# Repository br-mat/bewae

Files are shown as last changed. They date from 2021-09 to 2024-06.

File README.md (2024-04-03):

# Bewae - Bewässerungsprojekt v3.3

v3.3final versions are not stable (work in progress).

## About

Automatisiert Sensorgesteuerte Bewässerung mit Raspberry Pi & Arduino
<br>

**Ziele:**

+ Sensorgesteuerte Automatisierte Bewässerung der Balkonpflanzen
+ Speichern & Darstellung von Sensordaten
+ Überwachung & Steuerung von unterwegs
+ (Zukünftig) Abfrage von Wetterdaten & Bewässerung mit Machine Learning

## Inhalt:

- [Introduction (EN)](/README_EN.md)
- [Einleitung (DE)](#einleitung-de)
- [Steuerung des Systems](#steuerung-des-systems)
- [Setup](#setup)
- [Details](#details)
- [Bilder & Entstehung](#bilder--entstehung)

## Einleitung (DE)
Diese Version ist eher als Testversion zu sehen. <br>
Bei der bisherigen Aufarbeitung handelt es sich nicht um eine Schritt-für-Schritt-Anleitung. Es wird ein gewisses Grundwissen im Umgang mit Linux und Mikrokontrollern vorausgesetzt. Ziel ist es, lediglich einen Einblick in das Projekt zu geben und den Wiederaufbau im Frühjahr oder an neuen Standorten zu erleichtern. <br>

### Beschreibung

Zur Steuerung wird ein ESP-32 verwendet. Verschiedene Sensoren und Module erfassen eine Vielzahl von Daten, darunter Bodenfeuchtigkeits-, Temperatur-, Luftfeuchtigkeits- und Luftdruckdaten sowie Sonnenscheindauer. Diese Daten werden mithilfe eines InfluxDB-Clients an einen Raspberry Pi gesendet und in InfluxDB 2.0 gespeichert. <br>

Die Bewässerung folgt einem Zeitplan, der entweder mit vorprogrammierten Werten arbeitet oder über das Netzwerk gesteuert werden kann. Durch Einrichten eines VPNs (z.B. PiVPN) kann man auch von unterwegs seine Pflanzen im Auge behalten und bewässern. <br>

**Versorgung:**
Das System ist mit einem kleinen PV-Modul, einem Blei-Akku und einem kleinen 100l Wassertank ausgestattet. Je nach Temperatur muss nun nur noch einmal pro Woche daran gedacht werden, den Tank zu füllen. <br>

## Systemdiagramm

### V3.3 Abbildung:

 System Setup:                  | Solar Setup:
:-------------------------:|:-------------------------:
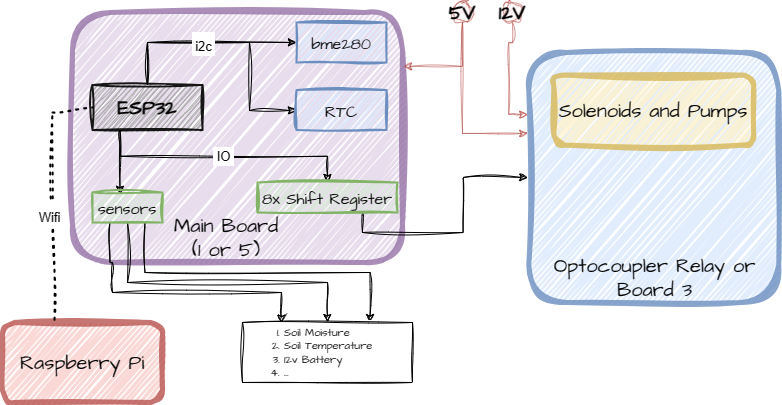
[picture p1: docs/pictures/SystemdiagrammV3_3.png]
System Systemdiagramm 3.3
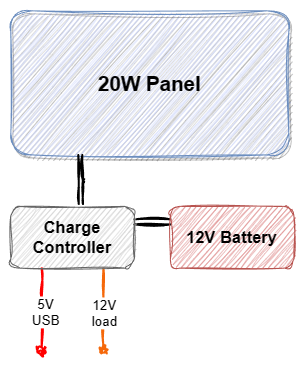
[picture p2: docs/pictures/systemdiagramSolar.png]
Solar Solar diagramm 3.3
 | 
zeigt grobe Skizzierung des Systems, Details zu Platinen siehe [(Details)](#details)

## Steuerung des Systems

### config.JSON

In dieser Datei befinden sich alle relevanten Einstellungen. Auf dem Controller wird diese Datei im Flash hinterlegt. Um auf Änderungen einfacher reagieren zu können, kann mit Node-Red (auf einem RaspberryPi) innerhalb des Netzwerks diese Datei zur Verfügung gestellt werden. Hierfür muss die Adresse in der connection.h angepasst werden.

Hinweis: Es ist auch möglich, ohne Verbindung zu einem RaspberryPi diese Datei zu verwenden, allerdings muss sie für Änderungen dann wieder neu aufgespielt werden.

### Steuerung der Bewässerung

Die Bewässerung wird mit den Einstellungen in der `config.JSON`-Datei gesteuert. Dabei werden zwei Variablen verwendet - timetable und water-time:

- 'timetable': Wird durch die ersten 24 Bit einer Integer-Zahl repräsentiert, wobei jedes Bit für eine Stunde des Tages steht. Um Platz zu sparen, wird es als Long Integer abgespeichert.
- 'water-time': Ist die Zeit (in Sekunden), die die jeweilige Gruppe bewässert wird. Hierbei können mehrere Ventile oder Ventil + Pumpe gleichzeitig gesetzt werden.

<br>

```cpp
// Beispiel-Zeitplan                           23211917151311 9 7 5 3 1
//                                              | | | | | | | | | | | |
unsigned long int timetable_default = 0b00000000000100000000010000000000;
//                                               | | | | | | | | | | | |
// Dezimale Darstellung: 1049600                22201816141210 8 6 4 2 0
//
```

Die Steuerung selbst kann auf folgenden Arten erfolgen:

- Config-Datei: Entweder lokal im Flash (SPIFFS), oder über Node-red bereitgestellt
- (currently not implemented) MQTT über W-LAN (App oder Pi) (noch nicht wieder implementiert)

<br>

Im File kann die Bewässerung wie im Beispiel unten konfiguriert werden:

```json
// JSON group template
{"group": {
    "Tomatoes": {         // name of grp
    "is_set":1,           // indicates status
    "vpins":[0,5],        // list of pins bound to group
    "water-time":10,      // water time in seconds
    "timetable":1049600,  // timetable (first 24 bit)
    "lastup":[0,0],       // runtime variable - dont touch!
    "watering":0          // runtime variable - dont touch!
    },
    .
    .
    .
  }
}
```

### Konfiguration der Sensoren:

Die Sensoren können mithilfe des `config.JSON` zu jeder Zeit verändert werden. Dabei sind einige Messfunktionen mit gängigen Sensoren implementiert. Es können auch noch Änderungen vorgenommen werden, um zurückgegebenen Werte zu modifizieren oder auch relative Messwerte (%) ausgegeben werden. <br>

Um einen Sensor korrekt zu konfigurieren ist es Notwendig eine Einzigartige ID als Json Key zu verwenden. Unter Diesem Key müssen noch 'name', 'field' und 'mode' vergeben werden. 'name' und 'field' entspricht dabei dem Eintrag in der DB unter dem der Messwert in InfluxDB zu finden ist. Implementierte 'mode' varianten können unten in der Tabelle entnommen werden, es kann erforderlich sein das noch weitere Dinge wie 'pin' etc. vorhanden sind.

Beispielkonfiguration:

```json
  "sensor": {
    "id00": {
      "name": "bme280",
      "field": "temp",
      "mode": "bmetemp"
    },
    .
    .
    .
    "id03": {
      "name": "Soil",
      "field": "temp",
      "mode": "soiltemp"
    },
    .
    .
    .
    "id08": {
      "name": "Soil",
      "field": "moisture",
      "mode": "vanalog",
      "vpin": 15,
      "hlim": 600,
      "llim": 250
    }
  },
  .
  .
  .
```

<br>

Konfiguration & Modifikatoren:
| Property | Description |
|---|---|
| `vpin` | Definiert Virtuellen Pin als input, für erweiterte Messfunktionen notwendig |
| `pin` | Definiert Normalen analogen Pin als input |
| `add` | (OPTIONAL) Addieren einer konstanten zum Ergebnis, optional wird nur bei >0 |
| `fac` | (OPTIONAL) Multiplizieren einer konstanten zum Ergebnis, optional wird nur bei >0 |
| `hlim` | (OPTIONAL) Obergrenze für relative Messung (%), optional wird nur bei >0 berücksichtigt |
| `llim` | (OPTIONAL) Untergrenze für relative Messung (%), optional wird nur bei >0 berücksichtigt |

<br>

Messfunktionen: <br>
| Measuring Mode | Description | Requirements |
|---|---|---|
| `analog` | reads analog pin | configured 'pin' in config.JSON |
| `vanalog` | reads virtual analog pin | configured 'vpin' in config.JSON |
| `bmetemp` | reads temperature from bme280 Sensor on Default address | Connected BME280 |
| `bmehum` | reads humidity from bme280 Sensor on Default address | Connected BME280 |
| `bmepress` | reads pressure from bme280 Sensor on Default address` | Connected BME280 |
| `soiltemp` | reads temperature from ds18b20 sensor from default 1 wire pin | Board need to have 1wire pin & connected Sensor |

<br>

## Setup Guide

### Mikrokontroller ESP32:

[Esp32 Code](./code/esp_32ard_bewae/) <br>

#### PlatformIO IDE

Stellen Sie zunächst sicher, dass PlatformIO in Visual Studio Code installiert ist. Dafür drücken Sie das 'Extensions' Icon in der linken Taskleiste und installieren 'PlatformIO IDE'. <br>

Öffnen Sie dann den Projektordner 'bewae' in VS Code. Schließen Sie als Nächstes Ihren ESP-32-Controller an. Zum Hochladen des Codes auf den ESP32 klicken Sie auf das Pfeilsymbol in der PlatformIO-Taskleiste. Das Gerät sollte automatisch erkannt werden, es kann nötig sein, die Boot-Taste während des Upload-Vorgangs zu drücken. Weiterhin ist es wichtig, das 'Filesystem' hochzuladen, dies kann mit dem Unterpunkt 'Upload Filesystem Image' der PlatformIO-Erweiterung gemacht werden. <br>

#### Config & WIFI (Optional)

Nun ist es wichtig, in den Dateien `connection.h` seine Zugangsdaten für das lokale Netzwerk einzutragen. <br>
Ebenfalls wären die IP des Systems worauf Node-red und die Datenbank installiert zu ändern. Sowie die dazugehörigen Daten. <br>
Weiters könnte noch die Adresse des Zeitservers zu ändern sein.  <br>

Für den Fall, dass keine Netzwerkverbindung möglich ist, sollte das Programm trotzdem funktionieren. Die Anpassung der Einstellungen ist dann allerdings schwieriger, da jedes Mal bei Änderungen das FileSystem neu hochgeladen werden muss. Außerdem muss die Zeit dann ebenfalls manuell gesetzt werden! Hierzu gibt es in der Helferklasse eine Funktion set_time. <br>

#### Config Hardware

Für die verschiedenen PCB-Layouts existieren unterschiedliche Hardware-Klassen. Diese leiten sich von der Helper-Klasse ab und schaffen eine Abstraktion der verwendeten Hardware. Dadurch wird es in Zukunft einfacher, andere Boards und sogar Mikrocontroller in das System zu integrieren.

Um die Konfiguration zu ändern, passen Sie bitte die folgenden Zeilen an Ihr verwendetes Board an:

##### ``main.cpp``
```cpp
// Initialisierung der Hardware Helper-Klasse
Helper_ExampleBoard HWHelper;
//Helper_config1_Board5v5 HWHelper;
```

##### ``Helper.h``
```cpp
// allowing to use HelperClass without having to create an instance of the class
extern ExampleBoard HWHelper;
```

Die verfügbaren Boards mit ihren Spezifikationen können Sie weiter unten finden.

### Raspberrypi

InfluxDB 2.0 benötigt ein 64-Bit-OS. Daher verwende ich einen Raspberry Pi 4B mit einem vollwertigen 64-Bit-Image.

#### Node-Red

How to [install](https://nodered.org/docs/getting-started/raspberrypi). <br>

Im Browser Your.Raspberry.Pi.IP:1880 Benutzer einrichten bzw. einloggen. Dann kann über das Web-Interface der [flow](/node-red-flows/flows.json) importiert werden. <br>
Öffnen Sie den Flow und klicken Sie doppelt auf den orangefarbenen 'read config'-Knoten. Ändern Sie den Pfad zu dem Pfad Ihrer Konfigurationsdatei.

#### InfluxDB 2.0

How to [install](https://docs.influxdata.com/influxdb/v2/install/?t=Raspberry+Pi). <br>
Influx kann auf zwei Arten aufgesetzt werden, entweder über das UI oder das CLI, Beschreibung dazu kann online gefunden werden (install link):

Set up InfluxDB through the UI
- With InfluxDB running, visit http://localhost:8086
- Click Get Started
- Set up your initial user
- Enter a Username for your initial user.
- Enter a Password and Confirm Password for your user.
- Enter your initial Organization Name.
- Enter your initial Bucket Name.
- Click Continue.

Die Berechtigungen für Buckets können recht einfach über das UI eingestellt werden und dazu dann ein Token generiert werden.

- In der Option 'Load Data' auf 'API TOKENS' klicken
- Klicken Sie auf 'Generate API TOKEN' -> Custom API Token
- Token-Beschreibung eingeben und Berechtigung (Write) wählen -> Auf 'Generate' klicken
- InfluxDB-Token nun in der `connection.h`-Datei ersetzen

---

Nun sollte alles vorbereitet sein. Die Konfigurationsdatei (`config.JSON`) kann nach Bedarf angepasst werden, dazu einfach die benötigten Funktionen (siehe Tabellen) wie im Beispiel gezeigt konfigurieren. <br>

Falls ein Relais-Modul verwendet wird mit invertierter Logik besteht die Option, die Ausgänge des Shift Registers zu invertieren, dazu in der `config.h`-Datei INVERT_SHIFTOUT auf true setzen. <br>
Weiterhin können noch Flags gesetzt werden, die das Debugging erleichtern. <br>

## Details

### Platinen

Die Schaltungen wurden mit Fritzing erstellt, die Steckbrettansicht bietet gute Übersicht und eignet sich ideal für Prototypen. Ab einer gewissen Größe des Projekts ist Fritzing allerdings nicht mehr ideal. Gerber-Dateien sind vorhanden. Für die Fritzing-Dateien ist lediglich die Platinenansicht relevant. Alle Boards verwenden den ESP-32 als Mikrocontroller. <br>

 Board 1:                  | Board 3:                  | Board 5:
:-------------------------:|:-------------------------:|:-------------------------:
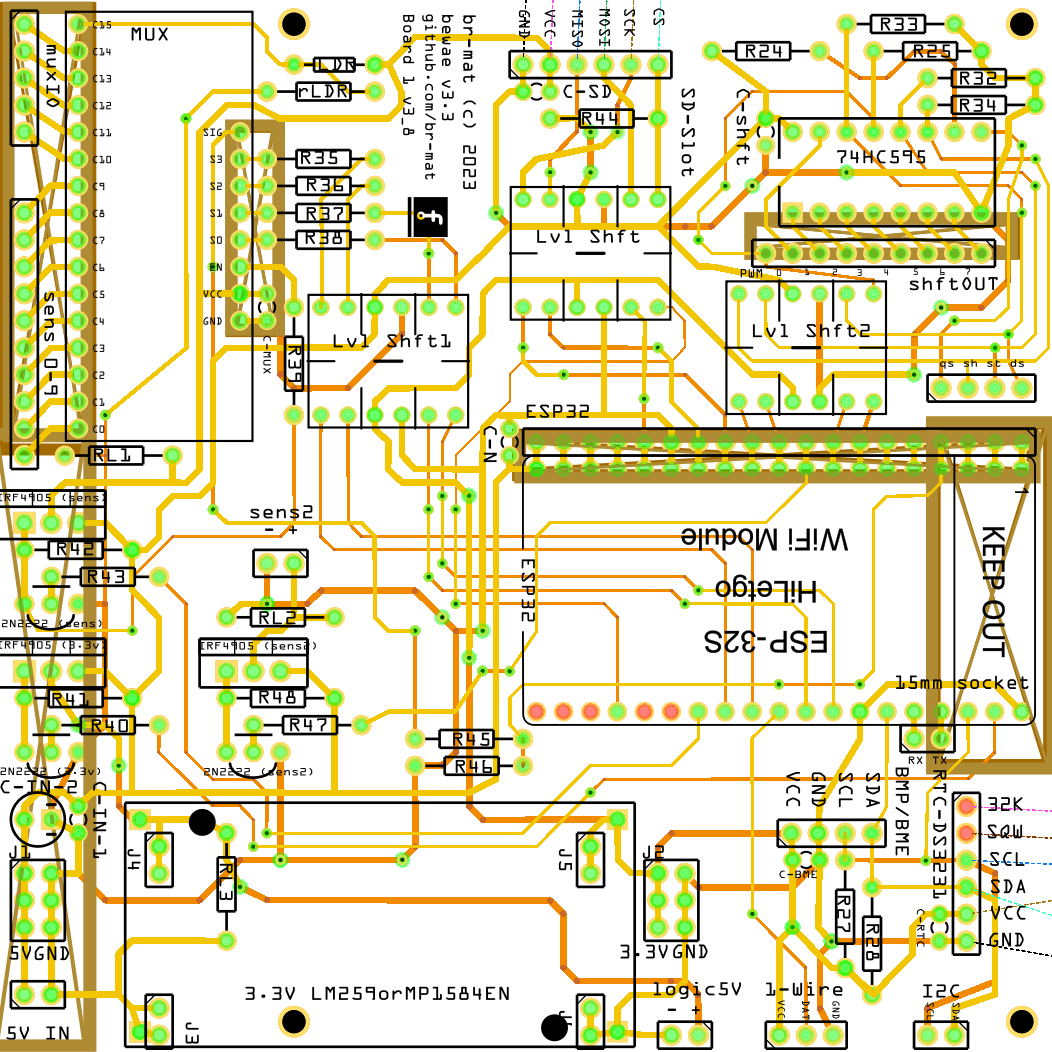
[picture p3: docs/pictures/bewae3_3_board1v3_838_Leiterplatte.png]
Board1
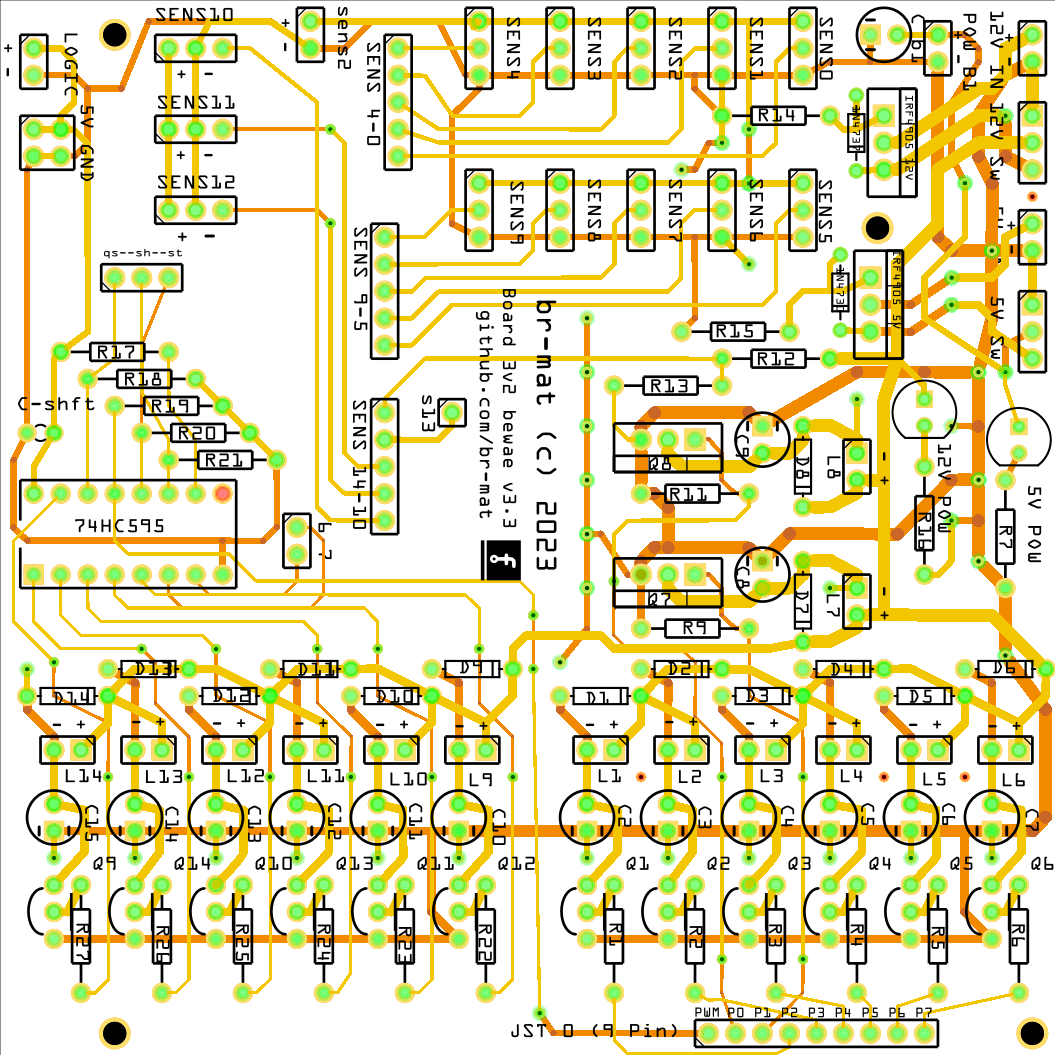
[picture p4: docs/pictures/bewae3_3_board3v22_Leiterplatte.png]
Board3
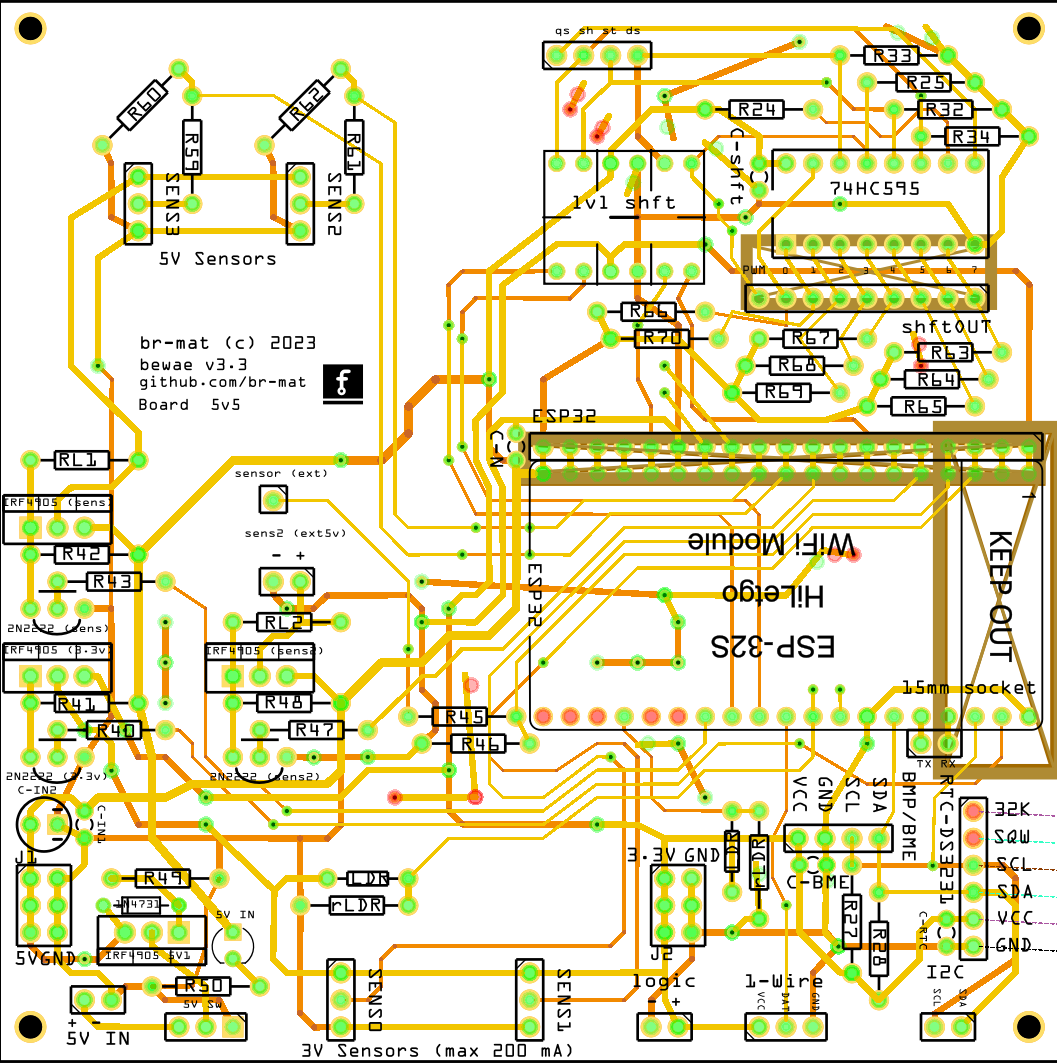
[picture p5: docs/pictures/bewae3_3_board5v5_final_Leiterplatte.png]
Board5
 |  | 
Main Board (Älteres testboard) | Extention Board | Main Board (neustes) <br> 

Steuerung der Ventile entweder über Optokoppler Relais (bis zu 8x mit adaption mehr) oder externe Beschaltung Board 3 und ähnliche. Die Ansteuerung ist über das Schieberegister (74hc595) vorgesehen.

#### **bewae3_3_board1v3_838.fzz** Hauptplatine (PCB)

Große Hauptplatine. Erfordert Board 3 oder externe Beschaltung für große Anzahl an analoger Sensoren. <br> Platz für bis zu 16 analoge Sensoren sowie BME280- und RTC-Modul über I2C. 8 Pins für Ventile/Pumpen (erweiterbar). Diese können entweder über Relais oder dem PCB Board 3 einfach verwendet werden.<br>

#### **bewae3_3_board3v22.fzz** als Erweiterung (PCB)

Als Erweiterung gedacht. Hat den Zweck, Steckplätze für Sensoren und weitere Verbraucher bereitzustellen. Zur Erweiterung der 8 Pins der Hauptplatine kann das Schieberegister verwendet werden. Insgesamt 16 Steckplätze für Sensoren inklusive Versorgung, sowie 2 Pumpen (*12V*) und 10 kleinere Ventile (*12V*).<br>

#### **bewae3_3_board5v5_final.fzz** als Hauptplatine (PCB)

Kleinere Hauptplatine (neueste). bietet die möglichkeit für eine Begrenzte anzahl an analogen Sensoren direkt am Board.
Verzichtet jedoch auf eine größere Anzahl an (analogen) Sensoranschlüssen. <br> 8 Pins für Ventile/Pumpen (mit Schieberegister erweiterbar). Platz für 2x 5V Sensoren, 2x 3V Sensoren, 1x LDR, I2C-Bus, 1-Wire-Bus. BME280- und RTC-Modul sind ebenfalls vorgesehen.<br>

### aktueller Aufbau

- ESP32 Board 1 & 3; Esp32 Board 5
- RaspberryPi 4 B (4GB)
- 10 Ventile 12V
- 2 Pumpen (aktuell nur eine 12V im Betrieb)
- 16 Analoge/Digitale Pins für Sensoren & andere Messungen (Bodenfeuchte, Photoresistor, etc.)
- BME280 Temperatur/Luftfeuchtigkeit/Druck Sensor
- RTC DS3231 Real Time Clock
- Bewässerungs Kit: Schläuche, Sprinkler, etc.
- 20W 12V Solar Panel
- 12 Ah 12V Bleiakku
- Solarladeregler

## Bilder & Entstehung

**Entstehung:** <br>

Das Projekt entstand aus einer mehrwöchigen Abwesenheit, während der die Balkonpflanzen ohne Versorgung gewesen wären. Die Pflanzen sollten mithilfe eines Bewässerungssets, Schläuchen, ein paar Düsen und einer Pumpe am Leben gehalten werden. Eine reguläre Bewässerung wie bei einer Zeitschaltuhr erschien mir jedoch zu langweilig, und mein Interesse an einem kleinen Bastelprojekt war geweckt. Kapazitive Bodenfeuchtesensoren und 4 kleine 12V Ventile wurden schnell bestellt, da ich zu Hause genügend Arduinos hatte. So kam es innerhalb einer Woche zur [Version 1](#v1), und das Überleben der Pflanzen war gesichert. Aus der Not heraus entstand ein Projekt, das mich eine Weile beschäftigte, und durch kontinuierliche Erweiterung und Verbesserung erfüllt es nach momentanem Stand weit mehr, als ursprünglich geplant. <br>
<br>

Zum Abschluss eine kleine Sammlung von Fotos über mehrere Versionen des Projekts, die im Laufe der Zeit entstanden sind:

### V3

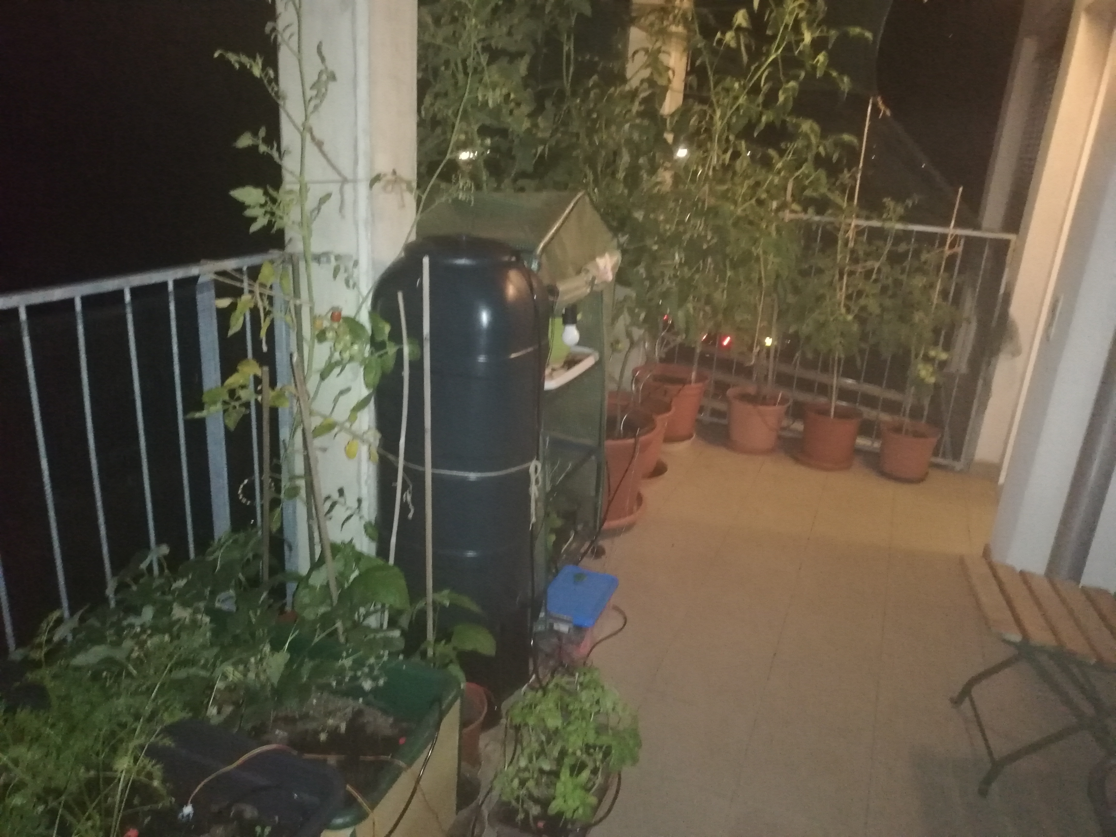
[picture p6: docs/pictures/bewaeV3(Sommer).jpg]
Bild
 <br>
Bild <br>
Bild <br>
Bild <br>

### V2

Bild <br>

### V1

Bild <br>
Bild <br>

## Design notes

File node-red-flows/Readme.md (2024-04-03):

flows.json:
This flow hosts a file to get request it.
In order to use flows.json you have to change the paths where the file is located.

bewaeConfigPageFlow.json:
This hosts a config web page where you can add and change values.
Change the path of the files of write and read -file nodes.

The flow contains a page to host the config file. (replacing older flows.json implementation)

Check for any other necessary changes.

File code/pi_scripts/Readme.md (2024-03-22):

This document provides a brief overview of how to use the following scripts. They are designed to run on a Raspberry Pi or a similar device using crontab.

1. store_weather_data.py:
   - This script collects data from OpenWeatherMap and stores it in a local InfluxDB instance (version 2.x).
   - Note: It is currently not required for functionality.

2. estimate_water_loss.py:
   - The purpose of this script is to retrieve forecast data from OpenWeatherMap.
   - It calculates an estimated total evaporation loss in milliliters per hour.
   - This function is intended to be executed daily.
   - The results can be used to automate plant irrigation if configured correctly, considering plant size and soil area.

3. hourlisttoBIN.py (to be removed soon):
   - This script converts a list of hours into a single number, which is used in the timetable.

4. old-config-to-JSON.py (to be removed soon):
   - Use this script to convert an old configuration format to the new one.

Additional files:
5. irrigation_example.JSON: This file provides an example configuration for the irrigation system.

6. monitoring_config.JSON: In this file, you can fill in details about the connection to InfluxDB, API keys, and other relevant settings.

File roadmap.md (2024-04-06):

This is a small roadmap to help me remember what I am working on.

To-do:
- Implement config web page (RaspberryPi)
- Integrate new configuration into the system (ESP32)
- Add OpenWeather forecast script to the Pi
- Reimplement dynamic watering controlled by Raspberry Pi
- Updated documentation

Open problems:
- Sensor rail needs 5V, not 3V! (Currently hooked onto logic switch 3.3V)

Future ideas:
- Add display and interface menu
- Using machine learning to controll watering process based on collected data
- Implement an app (configuration of sensors and groups)
- Add option to upload config file via bluetooth

Changes:
- Added OpenWeather scripts (saving current conditions and air condition to InfluxDB)
- Added corresponding .sh launcher files
- Added ESP32 build
- Added a second circuit to handle pumps and solenoids
- Updated (and tested) main circuit, corrected bugs and problems on ESP32 build
- Updated English translation of new version
- Added a new IrrigationController class
- Implemented a config file system using SPIFFS
- Implemented HTTP GET functionality to update config file
- Added Node-RED flow to provide config file
- Reworked circuit boards included new ones
- fixed reverse voltage protection
- Removed SD slot

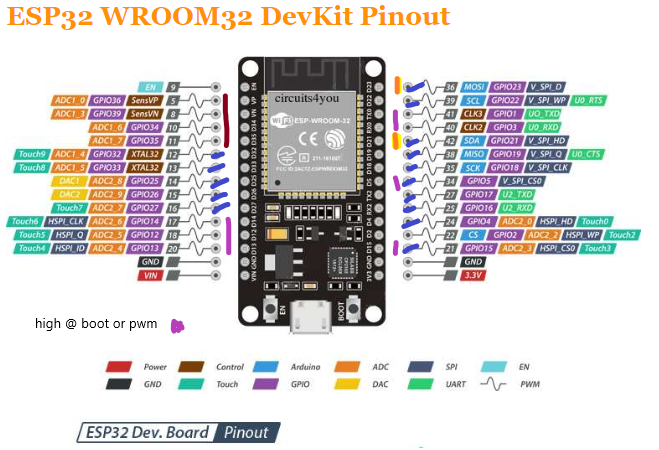
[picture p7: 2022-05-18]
code/esp_32ard_bewae/esp32-wroom-pinout-project.PNG

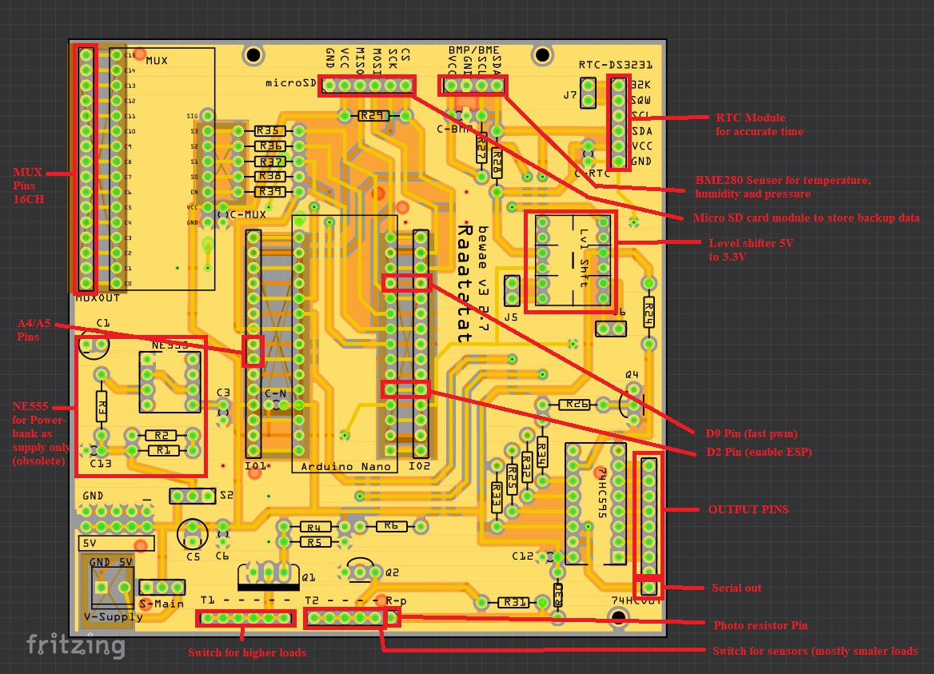
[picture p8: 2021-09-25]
docs/pictures/bewae_v3_1.png

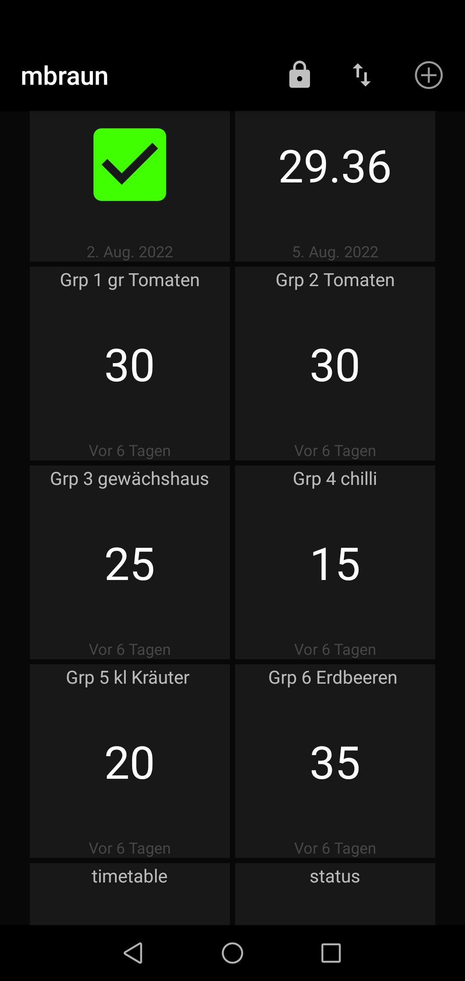
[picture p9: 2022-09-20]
docs/pictures/watering-config.jpg

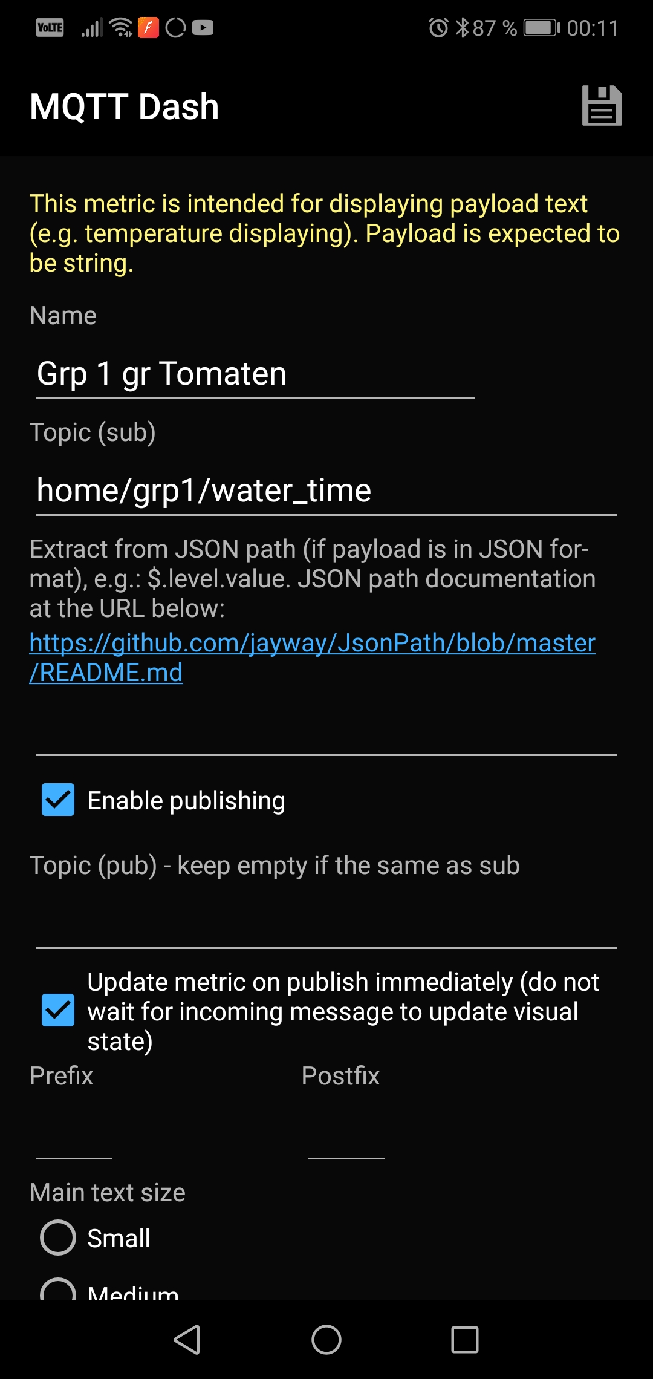
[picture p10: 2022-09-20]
docs/pictures/mqtt-app.jpg

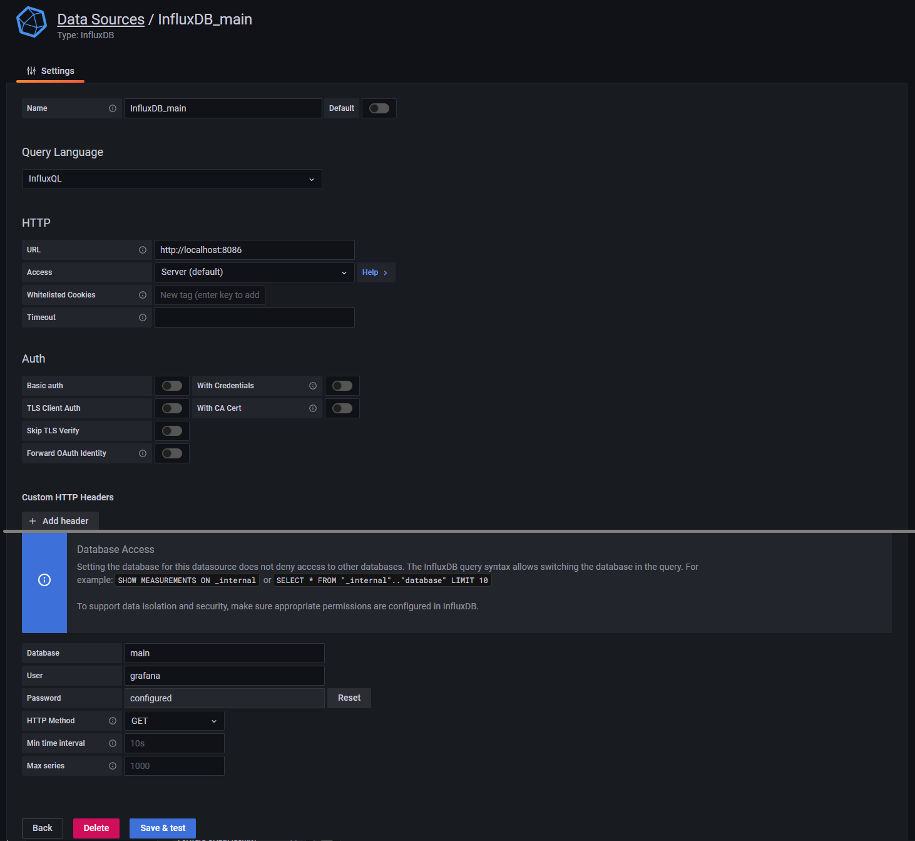
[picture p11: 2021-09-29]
docs/pictures/datasources.png

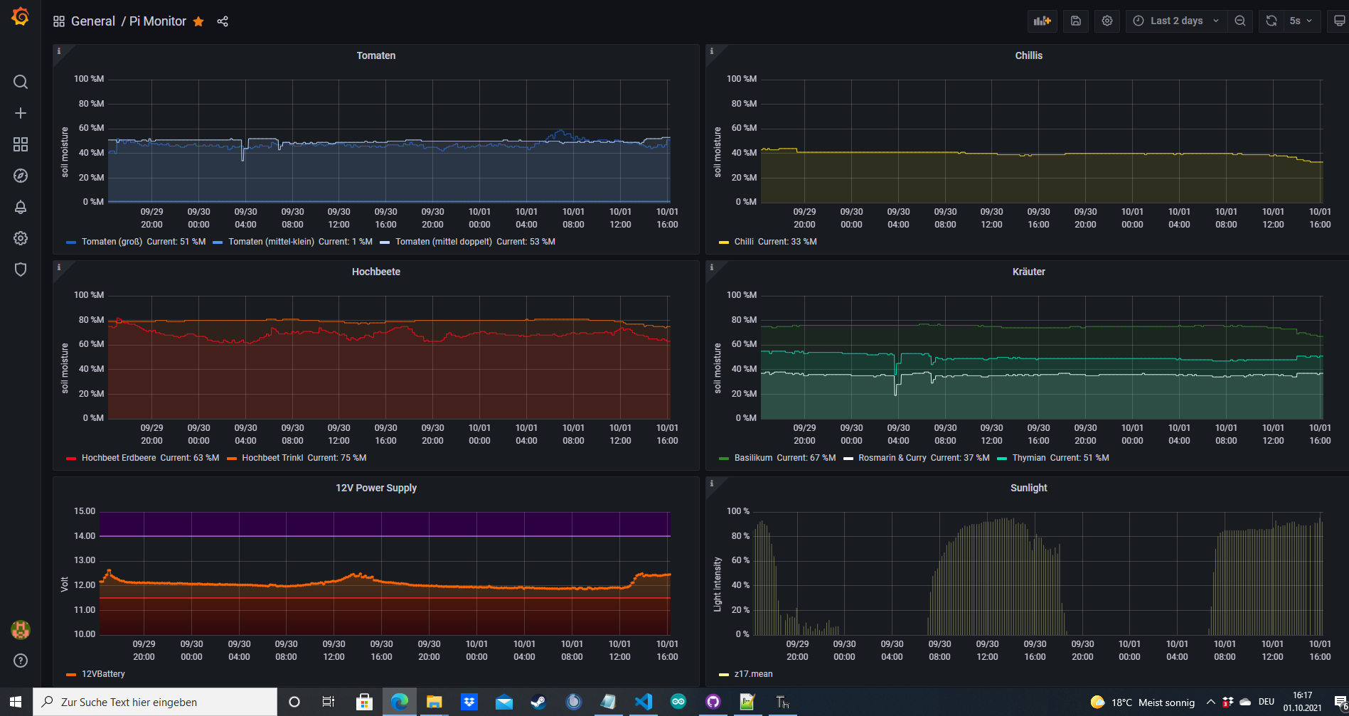
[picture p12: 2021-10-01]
docs/pictures/grafanarainyday.png

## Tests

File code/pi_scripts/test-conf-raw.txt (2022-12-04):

group
99 master 0 0
0 Tom1 100 0
1 Tom2 80 0
2 Gewa 30 0
3 Chil 40 0
4 Krtr 20 0
5 Erdb 50 0

switches
sw6 1
sw0 1
sw1 0
sw2 0

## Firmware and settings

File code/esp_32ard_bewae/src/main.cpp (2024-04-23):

////////////////////////////////////////////////////////////////////////////////////////////////////////////////////////
//
// br-mat (c) 2023
// email: matthiasbraun@gmx.at
//
// This is the main source file for the irrigation system. It is responsible for monitoring all sensor values,
// handling the watering procedure, and communicating with the Raspberry Pi to get and send data.
//
////////////////////////////////////////////////////////////////////////////////////////////////////////////////////////

//Standard
#include <Arduino.h>
#include <Wire.h>
#include <SPIFFS.h>
#include <OneWire.h>

//external
#include <Adafruit_Sensor.h>
#include <Adafruit_BME280.h>
#include <WiFi.h>
#include <PubSubClient.h>
#include <ArduinoJson.h>
#include <DallasTemperature.h>

//custom
#include <connection.h>
#include <Helper.h>
#include <IrrigationController.h>
#include <SensorController.h>
#include <SwitchController.h>
#include <config.h>

using namespace std;

//######################################################################################################################
//----------------------------------------------------------------------------------------------------------------------
//---- GLOBAL VARIABLES AND DEFINITIONS --------------------------------------------------------------------------------
//----------------------------------------------------------------------------------------------------------------------
//######################################################################################################################
//important global variables
//byte sec_; byte min_; byte hour_; byte day_w_; byte day_m_; byte mon_; byte year_; // containing time variables

struct tm oldtimeMark; // timemark

unsigned long nextActionTime = 0; // timestamp variable

bool thirsty = false; // marks if a watering cycle is finished

//timetable example
//                                             2523211917151311 9 7 5 3 1
//                                              | | | | | | | | | | | | |
//unsigned long int timetable_default = 0b00000000000000000000010000000000;
//                                               | | | | | | | | | | | | |
//                                              2422201816141210 8 6 4 2 0
unsigned long int timetable = 0; // holding info at which hour system needs to do something

// Setup a oneWire instance to communicate with any OneWire device
OneWire oneWireGlobal(oneWireBus);

// Pass our oneWire reference to Dallas Temperature sensor 
DallasTemperature soilsensorGlobal(&oneWireGlobal);

// use I2C interface
Adafruit_BME280 bme;

// initialise WiFi
WiFiClient wificlient;

// initialise Hardware Helper class
Helper_config1_Board5v5 HWHelper;
//Helper_config1_Board5v5 HWHelper;

// Create a BasicSensor instance
BasicSensor Sensors(&HWHelper, &bme, soilsensorGlobal);

// Create an instance of the InfluxDBClient class with the specified URL, database name and token
InfluxDBClient influx_client(INFLUXDB_URL, INFLUXDB_ORG, INFLUXDB_DB_NAME, INFLUXDB_TOKEN);

//######################################################################################################################
//----------------------------------------------------------------------------------------------------------------------
//---- SOME ADDITIONAL FUNCTIONS ---------------------------------------------------------------------------------------
//----------------------------------------------------------------------------------------------------------------------
//######################################################################################################################

// Task implementation can be found on bottom of code

// containing irrigation implementation, returns false if irrigation finished else true
bool irrigationTask();
// sensoring implementation, returns timestamp of next event in UL
long sensoringTask();
// powering down system, returning false when theres something to do else true!
bool checkSleepTask();

//######################################################################################################################
//----------------------------------------------------------------------------------------------------------------------
//---- SETUP -----------------------------------------------------------------------------------------------------------
//----------------------------------------------------------------------------------------------------------------------
//######################################################################################################################

void setup() {
///////////////////////////////////////////////////////////////////////////////////////////////////////////////////////////
// init
///////////////////////////////////////////////////////////////////////////////////////////////////////////////////////////
  //setCpuFrequencyMhz(80);
  // configure low power timer
  esp_sleep_enable_timer_wakeup(TIME_TO_SLEEP * uS_TO_S_FACTOR);

///////////////////////////////////////////////////////////////////////////////////////////////////////////////////////////
// configure pin mode
///////////////////////////////////////////////////////////////////////////////////////////////////////////////////////////
  HWHelper.setPinModes();

///////////////////////////////////////////////////////////////////////////////////////////////////////////////////////////
// initialize serial
///////////////////////////////////////////////////////////////////////////////////////////////////////////////////////////
  Serial.begin(9600);
  delay(1);
  #ifdef DEBUG
  Serial.println("Hello!");
  #endif

///////////////////////////////////////////////////////////////////////////////////////////////////////////////////////////
// initialize SPIFFS
///////////////////////////////////////////////////////////////////////////////////////////////////////////////////////////
  if (!SPIFFS.begin(true)) {
    #ifdef DEBUG
    Serial.println(F("An Error has occurred while mounting SPIFFS"));
    #endif
    return;
  }
  #ifdef DEBUG
  unsigned int totalBytes = SPIFFS.totalBytes();
  unsigned int usedBytes = SPIFFS.usedBytes();
  Serial.print("Total space: ");
  Serial.println(totalBytes);
  Serial.print("Used space: ");
  Serial.println(usedBytes);
  #endif

  /*
  fs::File file = SPIFFS.open(CONFIG_FILE_PATH);
  if(!file){
    #ifdef DEBUG
    Serial.println("Failed to open file for reading");
    #endif
    return;
  }
  file.close();*/

///////////////////////////////////////////////////////////////////////////////////////////////////////////////////////////
// initialize bme280 & ds18b20 sensor
///////////////////////////////////////////////////////////////////////////////////////////////////////////////////////////
  HWHelper.enablePeripherals();
  HWHelper.enableSensor();

  // test bme280
  delay(300); // giving some time to handle powerup of devices

  #ifdef DEBUG
  Serial.println(F("BME280 Sensor event test"));
  if (!bme.begin(BME280_I2C_ADDRESS)) {
    Serial.println(F("Warning: Could not find a valid BME280 sensor, check wiring!"));
  }
  else{
    float temp_test = bme.readTemperature();
    Serial.print(F("Temperature reading: ")); Serial.println(temp_test);
  }
  delay(10);

  // test ds18b20
  soilsensorGlobal.begin();
  delay(100);

  // Request temperature
  soilsensorGlobal.requestTemperatures();
  delay(5);
  // Read temperature from DS18B20 sensor
  float temperatureC = soilsensorGlobal.getTempCByIndex(0);
  Serial.print("Test DS18B20: "); Serial.println(temperatureC);
  #endif

///////////////////////////////////////////////////////////////////////////////////////////////////////////////////////////
// init time and date
///////////////////////////////////////////////////////////////////////////////////////////////////////////////////////////
  HWHelper.wakeModemSleep();
  delay(1);
  //uncomment if want to set the time (NOTE: only need to do this once not every time!)
  //HWHelper.set_time(00,56,18,01,11,9,23);
  //seting time (second,minute,hour,weekday,date_day,date_month,year)
  struct tm localTime = HWHelper.readTimeNTP();

  // automatically set time (requires WIFI access!!)
  struct tm local = HWHelper.readTimeNTP();
  if(HWHelper.verifyTM(local)){
    #ifdef DEBUG
    Serial.println(F("Info: Synched time!"));
    #endif
    HWHelper.setTime(local);
  }
  #ifdef DEBUG
  else{
    Serial.println(F("Setup Warning: Could not verify time!"));
  }
  #endif

  delay(100);
  //initialize global time
  bool condition = HWHelper.readTime(&oldtimeMark);
  delay(30);

///////////////////////////////////////////////////////////////////////////////////////////////////////////////////////////
//init Irrigation Controller instance and update config
///////////////////////////////////////////////////////////////////////////////////////////////////////////////////////////
  HWHelper.wakeModemSleep();
  delay(1);
  // update the config file stored in spiffs
  // in order to work a RasPi with node-red and configured flow is needed
  HWHelper.syncConfig();
  // TEST DEVICE CONFIGURATION
  SwitchController status_switches(&HWHelper); // initialize switch class

Serial.print("Free heap memory: ");
Serial.println(ESP.getFreeHeap());
Serial.print("Test DEVICE CONFIG!");
DynamicJsonDocument doc(512);
Serial.print("Free heap memory: ");
Serial.println(ESP.getFreeHeap());
String p = IRRIG_CONFIG_PATH; // Make sure IRRIG_CONFIG_PATH is defined somewhere
String p2 = JSON_SUFFIX;
String filePath = p + p2; // Concatenate to form the file path
DynamicJsonDocument jsonDoc = HWHelper.readConfigFile(filePath.c_str());
Serial.println("TESTING FILE RETURNS!");
Serial.println(jsonDoc.isNull());
String f_jsonDoc;
serializeJson(jsonDoc, f_jsonDoc);
Serial.println("Irrig file: ");
Serial.println(f_jsonDoc);

Serial.print("Free heap memory: ");
Serial.println(ESP.getFreeHeap());

  HWHelper.system_sleep(); //power down prepare sleep
  delay(100);

}

//######################################################################################################################
//----------------------------------------------------------------------------------------------------------------------
//---- MAIN PROGRAM LOOP -----------------------------------------------------------------------------------------------
//----------------------------------------------------------------------------------------------------------------------
//######################################################################################################################
void loop(){
////////////////////////////////////////////////////////////////////////////////////////////////////////////////////////
// start & sleep loop
////////////////////////////////////////////////////////////////////////////////////////////////////////////////////////

// manage sleep and updating of configuration
while(checkSleepTask()){
}
Serial.print(F("INIT SWITCHES:"));
SwitchController status_switches(&HWHelper); // initialize switch class
//status_switches.updateSwitches(); // get called when initialized

// print system status
#ifdef DEBUG
Serial.println(F("Config: ")); Serial.print(F("Main switch: ")); Serial.println(status_switches.getMainSwitch());
Serial.print(F("Irrigation switch: ")); Serial.println(status_switches.getIrrigationSystemSwitch());
Serial.print(F("Measurement switch: ")); Serial.println(status_switches.getDatalogingSwitch());
Serial.print(F("Timetable: ")); Serial.println(timetable, BIN);
#endif

////////////////////////////////////////////////////////////////////////////////////////////////////////////////////////
// collect & send data
////////////////////////////////////////////////////////////////////////////////////////////////////////////////////////
#ifdef DEBUG
Serial.print(F("Datalogphase: ")); Serial.println(millis() > nextActionTime);
Serial.print(F("Next action time: ")); Serial.println(nextActionTime);
#endif
//if(true)
if((status_switches.getDatalogingSwitch()) && (millis() > nextActionTime))
{
  // Sensoring implementation
  nextActionTime = sensoringTask() + measure_intervall; // sensoring task returns finishing timestamp
}
else{
  nextActionTime = millis() + measure_intervall *2; // set a min delay (2 times longer)
}

////////////////////////////////////////////////////////////////////////////////////////////////////////////////////////
// watering - return true if finished
////////////////////////////////////////////////////////////////////////////////////////////////////////////////////////
if(status_switches.getIrrigationSystemSwitch()){ // always enter checking, timing is handled by irrigation class
  irrigationTask();
}
#ifdef DEBUG
else{
Serial.print(F("Irrigation not set, satus: ")); Serial.println(status_switches.getIrrigationSystemSwitch());
}
#endif

////////////////////////////////////////////////////////////////////////////////////////////////////////////////////////
// end loop
////////////////////////////////////////////////////////////////////////////////////////////////////////////////////////

#ifdef DEBUG
Serial.println(F("--- End loop! ---"));
#endif
}
//######################################################################################################################
//----------------------------------------------------------------------------------------------------------------------
//---- MAIN PROGRAM END -------------------------------------------------------------------------------------------------
//----------------------------------------------------------------------------------------------------------------------
//######################################################################################################################



////////////////////////////////////////////////////////////////////////////////////////////////////////////////////////
// sensoring - returns timestamp of next event
////////////////////////////////////////////////////////////////////////////////////////////////////////////////////////
long sensoringTask(){
  #ifdef DEBUG
  Serial.println();
  Serial.println(F("enter datalog phase"));
  #endif

  if(!PUBDATA){
    #ifdef DEBUG
    Serial.println();
    Serial.println(F("Not mearuring Data! Flag set to false."));
    #endif
    return millis();
  }

  // turn on additional systems
  HWHelper.enablePeripherals();
  HWHelper.enableSensor();
  // shutdown wifi to free up adc2 pins!
  HWHelper.disableWiFi();
  delay(500); // give time to balance load

  // Create data vector to collect and publish later
  std::vector<SensorData> dataVec;
  std::vector<SensorData> dataVecTest;

  DynamicJsonDocument configf(CONF_FILE_SIZE);
  String path = String(SENS_CONFIG_PATH) + String(JSON_SUFFIX);
  configf = HWHelper.readConfigFile(path.c_str());
  JsonObject obj;

  //float test = Sensors.onewirehandler();
  //Serial.print("ds18b20 temp: "); Serial.println(test);

  // handle analog pins
  obj = configf.as<JsonObject>();

  if(obj){
    for (JsonObject::iterator it = obj.begin(); it != obj.end(); ++it){
      String id = it->key().c_str();
      JsonObject sensorConfig = it->value().as<JsonObject>();
      // create & fill data
      SensorData data = Sensors.measurePoint(&HWHelper, id, sensorConfig);
      // Add the new SensorData object to the vector
      dataVecTest.push_back(data);
    }
  }

  // reconnect to wifi
  HWHelper.connectWifi();
  // Publish data vector
  bool success = Sensors.pubVector(&influx_client, dataVecTest);
  //bool success = false; //DEBUG
  #ifdef DEBUG
  if(success){
    Serial.println(F("All data published!"));
  }
  else{
    Serial.println(F("Warning: Problem occured while publishing data vector!"));
  }
  #endif

  // shut down addidional systems
  HWHelper.disablePeripherals();
  HWHelper.disableSensor();

  return millis(); // finishing timestamp
}



////////////////////////////////////////////////////////////////////////////////////////////////////////////////////////
// watering - return true if NOT fnished
////////////////////////////////////////////////////////////////////////////////////////////////////////////////////////
bool irrigationTask(){
//thirsty = true; //uncoment for testing only
  HWHelper.enablePeripherals();

  #ifdef DEBUG
  Serial.println(F("Enter watering phase"));
  #endif
  delay(30);

  // load config file
  String path = String(IRRIG_CONFIG_PATH) + String(JSON_SUFFIX);
  DynamicJsonDocument doc = HWHelper.getJsonDoc(path.c_str());
  JsonObject groups;
  // Check if the document is not null and contains a JsonObject
  if (doc.isNull() || !doc.is<JsonObject>()) {
    #ifdef DEBUG
    Serial.println(F("Warning: Configuration not valid!"));
    #endif
    return false;
  }
  groups = doc.as<JsonObject>();
  int numgroups = groups.size();
  // sanity check
  if (numgroups > max_groups) {
    #ifdef DEBUG
    Serial.println(F("Warning: too many groups! Exiting procedure"));
    #endif
    return false;
  }
  // check for valid object
  if (groups.isNull()) {
    #ifdef DEBUG
    Serial.println(F("Error: No 'Group' found in file!"));
    #endif
    return false; // break loop and continue programm
  }

  // load empty irrigationcontroller instances 
  IrrigationController Group[numgroups];
  int j = 0;

  // Iterate over each group and load the config
  for (JsonObject::iterator groupIterator = groups.begin(); groupIterator != groups.end(); ++groupIterator) {
    // Load schedule configuration for the current group
    if (String(groupIterator->key().c_str()) == String("checksum")){
      continue; // skip checksum (TODO: idea for rework of config files, then this "forbiden" name would be ok {"name"{config},"checksum":"asdfxcz"})
    }
    bool success = Group[j].loadScheduleConfig(*groupIterator);
    if (!success) { // if it fails reset class instance
      #ifdef DEBUG
      Serial.print(F("Error: Failed to load schedule, for: '["));
      Serial.print(groupIterator->key().c_str());
      JsonObject groupData = groupIterator->value();
      Serial.print(F("] data: "));
      serializeJson(groupData, Serial); Serial.println(F("'"));
      #endif
      // Reset the class to an empty state
      Group[j].reset();
      break;
    }
    /*
#ifdef DEBUG
Serial.print(F("Error: Failed to load schedule, for: '["));
Serial.print(groupIterator->key().c_str());
JsonObject groupData = groupIterator->value();
Serial.print(F("] data: "));
serializeJson(groupData, Serial); Serial.println(F("'"));
#endif*/
    // Increment j for the next group
    j++;
  }

  // --- Watering ---
  // description: trigger at specific time
  //              alternate the solenoids to avoid heat damage, let cooldown time if only one remains
  // Hints:  main mosfet probably get warm
  //         pause procedure when measure events needs to happen
  //         NEVER INTERUPT WHILE WATERING!
  ///////////////////////////////////////////////////////////////////////////////////////////////////////////////////////////
  while((nextActionTime > millis()) && (thirsty)){
    // process will trigger multiple loop iterations until thirsty is set false
    // this should allow a regular measure intervall and give additional time to the water to slowly drip into the soil
    delay(15);

    // Iterate over all irrigation controller objects in the Group array
    // This process will trigger multiple loop iterations until thirsty is set false
    int finStatus = 0;
    for(int i = 0; i < numgroups; i++){
      // ACTIVATE SELECTED GROUP
      //hour1 = 19 // change for testing

      // start watering selected group
      // it will check if the instance is ready for watering (or on cooldown)
      finStatus += Group[i].watering_task_handler();
      delay(500); // give little delay
    }

    // check if all groups are finished and reset status
    if(!finStatus){
      thirsty = false;
    }
    esp_light_sleep_start(); // sleep one period
  }

  HWHelper.disablePeripherals();
  HWHelper.disableSensor();

  return thirsty;
}
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

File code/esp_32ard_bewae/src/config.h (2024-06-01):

////////////////////////////////////////////////////////////////////////////////////////////////////////////////////////
//
// br-mat (c) 2022
// email: matthiasbraun@gmx.at
//
// Config file, setting constants and macros.
//
////////////////////////////////////////////////////////////////////////////////////////////////////////////////////////

#ifndef __CONFIG_H__
#define __CONFIG_H__


#define RasPi 1

#ifndef CONFIG_FILE_PATH
#define CONFIG_FILE_PATH "/config.JSON" //specifies name of config file stored within spiffs
#endif

#ifndef RUNNING_FILE_PATH
#define RUNNING_FILE_PATH "/running.Json"
#endif

#ifndef WEB_PREFIX
#define WEB_PREFIX "/bewae/get-config"
#endif

#ifndef DEVICE_CONFIG_PATH
#define DEVICE_CONFIG_PATH "/deviceConfig"
#endif

#ifndef IRRIG_CONFIG_PATH
#define IRRIG_CONFIG_PATH "/plantConfig"
#endif

#ifndef SENS_CONFIG_PATH
#define SENS_CONFIG_PATH "/sensorConfig"
#endif

#ifndef JSON_SUFFIX
#define JSON_SUFFIX ".Json"
#endif

#ifndef CONF_FILE_SIZE
#define CONF_FILE_SIZE 8192 // estimate at https://arduinojson.org/v6/assistant/#/step1
#endif

#ifndef MAX_GROUP_LENGTH
#define MAX_GROUP_LENGTH 20 //Max Group length
#endif


///////////////////////////////////////////////////////////////////////////////////////////////////////////////////////////
// Pin & Adress configuration
///////////////////////////////////////////////////////////////////////////////////////////////////////////////////////////
#ifndef DS3231_I2C_ADDRESS
#define DS3231_I2C_ADDRESS 0x68 //adress rtc module
#endif

#ifndef BME280_I2C_ADDRESS
#define BME280_I2C_ADDRESS 0x76 //adress bme module
#endif

#ifndef oneWireBus
#define oneWireBus 5 // GPIO where the DS18B20 is connected to
#endif


///////////////////////////////////////////////////////////////////////////////////////////////////////////////////////////
// default variable definitions & constants
///////////////////////////////////////////////////////////////////////////////////////////////////////////////////////////
// reverse shiftregister output in case of optocoupler (v-pins)
#ifndef INVERT_SHIFTOUT
#define INVERT_SHIFTOUT true // set true if using negative logic relais
#endif

// publish data flag (DEBUG FLAG)
#ifndef PUBDATA
#define PUBDATA true // set true if you dont want to pub data
#endif

// debug flag
#ifndef DEBUG
#define DEBUG 1
#endif

// debug spam flag (show all logged info)
#ifndef DEBUG_SPAM
//#define DEBUG_SPAM 1
#endif

// sensor field
#ifndef INFLUXDB_FIELD
#define INFLUXDB_FIELD "bewae-sensors"
#endif

// pump & transistor max on time
#ifndef max_active_time_sec
#define max_active_time_sec 40 //max time active of each solenoid ==> SECOND
#endif

#ifndef measure_intervall
#define measure_intervall 600000UL //~10 min, measurement intervall ==> MILLISECOND
#endif

#ifndef SOLENOID_COOLDOWN
#define SOLENOID_COOLDOWN 30000UL //min cooldown time of each solenoid ==> MILLISECOND
#endif

#ifndef DRIVER_COOLDOWN
#define DRIVER_COOLDOWN 50000UL // min cooldown of drivers and hardware (somewhat depending on max_active_time_sec)
#endif

// number of possible solenoids (v-pins)
#ifndef max_groups
#define max_groups 16
#endif

// time factors
#ifndef uS_TO_S_FACTOR
#define uS_TO_S_FACTOR 1000000 //Conversion factor for micro seconds to seconds
#endif

#ifndef TIME_TO_SLEEP
#define TIME_TO_SLEEP  8 //Time ESP32 will go to sleep (in seconds)
#endif

#ifndef measurement_LSB
#define measurement_LSB 0.01008018 //LSB in Volt! - REPLACE with your specific value, derives from voltage devider and
                                            //resolution of adc
#endif

#ifndef measurement_LSB5V
#define measurement_LSB5V 0.00151581243 //LSB in Volt! - REPLACE with your specific value, derives from voltage devider and
                                            //resolution of adc
#endif

// time & timezonerelated stuff
const int SECONDS_PER_HOUR = 3600;
const int gmtOffset_hours = 1;
const int daylightOffset_hours = 1;

#endif

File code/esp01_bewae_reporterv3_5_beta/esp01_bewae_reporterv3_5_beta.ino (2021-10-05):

//IIC SLAVE MQTT REPORTER
#include "PubSubClient.h" // Connect and publish to the MQTT broker
#include <Wire.h>
#include <String.h>

// Code for the ESP8266
#include <ESP8266WiFi.h> // Enables the ESP to connect to the local network (via WiFi)

//definitions
#define DEBUG

#define MAX_MSG_LEN (128)
#define max_groups 6

// iic
#define slave_adr 0x08 //adress of esp01
#define nano_adr 0x07 //adress of arduino nano


// WiFi
const char* ssid = "A1-08e52c";         // Your personal network SSID
const char* wifi_password = "mabritck"; // Your personal network password

// MQTT
const char* mqtt_server = "10.0.0.18";  // IP of the MQTT broker
//const char* topic_prefix_original="home/test/temperature";
String topic_prefix = "home/sens3/z";
const char* mqtt_username = "mbraun"; // MQTT username
const char* mqtt_password = "wdsaibuii123"; // MQTT password
const char* clientID = "client_test2"; // MQTT client ID
const char* humidity_topic_sens2 = "home/sens2/humidity";
const char* temperature_topic_sens2 = "home/sens2/temperature";
const char* pressure_topic_sens2 = "home/sens2/pressure";
const char* config_status = "home/bewae/config_status"; //send status with mqtt to raspberrypi

//subsciption topics
const char* watering_topic = "home/bewae/config";    //bewae config and config status indicate things not passed to influx recive watering instructions
const char* bewae_sw = "home/nano/bewae_sw";       //switching watering system no/off
const char* watering_sw = "home/nano/watering_sw"; //switching value override on/off (off - using default values on nano)
const char* testing = "home/test/tester";

bool data_collected = false; //confirms that all requested data has been collected and wifi can be shut down
bool update_data = false;            //check if nano requests config data update
bool new_data = false;
const int max_sens=28;
int int_data[max_sens] = {0}; //keep it as int array, in case all this is migrated to a single mcu and storage space becomes relevant again
                              //data stay comparable as a whole

//same value as in code for nano probably put base values here
byte statusbyte = 0;   //indicating status of collected data (111 all good ..)
int groups[max_groups] = {0};
byte sw0; //bewae switch
byte sw1; //water value override switch

// Initialise the WiFi and MQTT Client objects
WiFiClient wifiClient;
// 1883 is the listener port for the Broker
PubSubClient client(mqtt_server, 1883, wifiClient); 


void connect_MQTT(){
  // connet to the MQTT broker via WiFi
  WiFi.forceSleepWake();
  delay(1);
  WiFi.mode(WIFI_STA);
  delay(1);
  #ifdef DEBUG
  Serial.print("Connecting to ");
  Serial.println(ssid);
  #endif
  WiFi.begin(ssid, wifi_password);
  int tries = 0;
  while ((WiFi.status() != WL_CONNECTED) && (tries++ < 20)) {
    delay(500);
    #ifdef DEBUG
    Serial.print(" . ");
    #endif
    if(tries == 10) {
      WiFi.begin(ssid, wifi_password);
      #ifdef DEBUG
      Serial.print(F(" Trying again "));
      Serial.print(tries);
      #endif
      delay(2000);
    }
  }
  #ifdef DEBUG
  Serial.println("WiFi connected");
  Serial.print("IP address: ");
  Serial.println(WiFi.localIP());
  #endif
  // Connect to MQTT Broker
  // client.connect returns a boolean value to let us know if the connection was successful.
  // If the connection is failing, make sure you are using the correct MQTT Username and Password (Setup Earlier in the Instructable)
  if (client.connect(clientID, mqtt_username, mqtt_password)) {
    #ifdef DEBUG
    Serial.println("Connected to MQTT Broker!");
    #endif
    client.setCallback(callback);
    client.subscribe(watering_topic, 0); //(topic, qos) quality of service: qos 0 "fire and forget",
    client.subscribe(bewae_sw, 0);       // qos 1 confirm at least once, qos 2 double confirmation reciever
    client.subscribe(watering_sw, 0);
    client.subscribe(testing, 0);
    client.setCallback(callback);
  }
  else {
    #ifdef DEBUG
    Serial.println("Connection to MQTT Broker failed...");
    #endif
  }
}


byte transmitt_config(int16_t data[], byte len, byte stat){
  //this function sends instruction data with I2C to the arduino nano
  #ifdef DEBUG
  Serial.println("Transmitt process triggered");
  #endif
  if(len<32+1){ //max 32 bytes
    #ifdef DEBUG
    Serial.println(groups[5]);
    #endif
    byte rstatus = 0;
    byte bdata[(max_groups+2)*2+2]={0}; //max_group+2 --> all watering groups + 2 bool values; +2 extra bytes as framing
    bdata[sizeof(bdata)-1]=stat; //tail framing with fixed value for identification on nano
    memcpy(bdata+1, data, len);  //framing on begin of transmission -->0
    Wire.beginTransmission(nano_adr);
    Wire.write(bdata, sizeof(bdata));
    rstatus += Wire.endTransmission();
    #ifdef DEBUG
    Serial.print(F("Sent byte array is: "));
    for(int i=0;i<sizeof(bdata);i++){
      Serial.println(bdata[i]);
    }
    #endif
  }
  else{
    #ifdef DEBUG
    Serial.println(F("ERROR: transmitted array to big"));
    #endif
  }
}


void callback(char *topic, byte *payload, unsigned int msg_length){
  //callback function to receive mqtt data
  //watering topic payload rules:
  //',' is the sepperator -- no leading ',' -- msg end with ',' -- only int numbers
  #ifdef DEBUG
  Serial.print(F("Enter callbacktopic: "));
  Serial.println(topic);
  #endif
  // copy payload to a string
  String msg="";
  if(msg_length > MAX_MSG_LEN){ //limit msg length
    msg_length = MAX_MSG_LEN;
    #ifdef DEBUG
    Serial.print(F("Message got cut off, allowed: "));
    Serial.println(MAX_MSG_LEN);
    #endif
  }
  for(int i=0; i< msg_length; i++){
    msg+=String((char)payload[i]);
  }
  //trigger correct topic to decode msg
  if(String(watering_topic) == topic){
    int c_index=0;
    for(int i=0; i<max_groups; i++){
      String val="";
      int start_index = c_index;
      c_index=msg.indexOf(",",start_index)+1; //find point of digit after the sepperator ','
      if((int)c_index == (int)-1){            //index = -1 --> char nor found
        c_index=msg_length+1;      //add 1 to get full message range in case there is no ',' on payload end
      }
      //extracting csv values
      for(start_index; start_index<c_index-1; start_index++){
        val+=msg[start_index];
      }
      groups[i]=val.toInt();
      #ifdef DEBUG
      Serial.print(F("MQTT val received:"));
      Serial.println(val.toInt());
      Serial.print(F("index: "));
      Serial.println(i);
      #endif
    }
  }
  if(String(bewae_sw) == topic){
    sw0 = msg.toInt();
    #ifdef DEBUG
    Serial.println(F("watering switched"));
    #endif
  }
  if(String(watering_sw) == topic){
    sw1 = msg.toInt();
    #ifdef DEBUG
    Serial.println(F("watering-values switched"));
    #endif
    data_collected=true;
  }
}
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

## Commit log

2021-07-28 adding files
    move files from local project to github
    [Platine_01.fzz, bew_entwurf_v2_7.fzz]
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2021-10-22 updated structure
    improve readability of the repository
    [Platine_01.fzz, bew_entwurf_v2_7.fzz]
2021-11-16 Create Platine_02v1.fzz
    Extention PCB
    [Platine_02v1.fzz]
2022-01-18 added experimental openweather stuff
    This is the current state of a new feature, it is totally experimental and currently not included into the main project.
2022-05-04 adding new circuit version
    replacing arduino nano by esp32 & add 2nd Board
    [bewae3_3_board1v1.fzz, bewae3_3_board2v1.fzz]
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2022-05-18 added skeleton for esp32 build
    platformio folder containing info and skeleton structure of the project with esp32
2022-05-18 updated pcb boards
    [bewae3_3_board1v1.fzz, bewae3_3_board1v3_5.fzz, bewae3_3_board2v1.fzz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]
2022-05-19 reworked skeleton structure for esp32 build
    [config.h, main.cpp]
2022-06-21 updated board 2 circuit
    added pull up resistors to the logic ic's, because of their open collector nature
    [bewae3_3_board2v3.fzz, bewae3_3_board2v5.fzz]
2022-06-21 updated board 1 circuit
    [bewae3_3_board1v3_5.fzz, bewae3_3_board1v3_6.fzz]
2022-07-14 updated main circuit
    bugfixes, minor layout changes
    [bewae3_3_board1v3_7.fzz, bewae3_3_board2v6.fzz]
2022-07-14 correct bugs & problems on ESP32 build
    fixed bme280 reading problem
    [Helper.h, config.h, helper.cpp]
2022-07-18 reworked data transmission process
    using data structure instead of arrays
    [main.cpp]
2022-07-19 esp32 code updated
    reworked bme sensor implementation
    [config.h, helper.cpp, main.cpp]
2022-08-01 Update main.cpp
    fixed issue where new features where not executed properly
    [main.cpp]
2022-08-02 fixed issue
    issue regarding timetable feature
    [main.cpp]
2022-09-20 Update main.cpp
    fixed a problem with sleep duration
    [main.cpp]
2022-10-19 added configuration from JSON file
    using and testing new comms functionality on esp32, improved readability of code, changed JSON config file generator
2022-11-07 Delete bewae-config.txt
    outdated file
    [bewae-config.txt]
2022-11-09 clean up
    delete old arduino nano build, esp32 version is further ahead now
2022-11-09 remove old arduino build
    [Platine_01.fzz, Platine_02v1.fzz, bew_entwurf_v2_7.fzz]
2022-11-17 Update main.cpp
    implement new timetable feature on the MC, prepare SPIFFS to possibly hold config file so data can be stored even when power goes down for some reason or wifi looses connection
    [main.cpp]
2022-12-04 added SPIFFS config feature
    Save and load config from a json format config file from flash, using SPIFFS. Reworked old concept.
    [Helper.h, helper.cpp, main.cpp]
2022-12-19 Update IrrigationController.cpp
    fixing a problem causing and error
    [IrrigationController.cpp]
2022-12-20 Updated header
    Expanded the header in the files to include a short description of the program and its functionality, as well as a list of dependencies.
    [Helper.h, IrrigationController.cpp, config.h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]
2022-12-23 Added waterOn function to start watering process
    Implemented waterOn function in IrrigationController class to control irrigation process based on current time and readiness of hardware.
2022-12-23 Update helper.cpp
    Added a check for an error when reserializing a Json file.
    [helper.cpp]
2022-12-25 Updating IrrigationController class
    Adding a new member function to this class which should return a summed timetable.
    Also changed activation such that it is possible with only a pump or a solenoid to use these methods.
    Changed struct in order to let it count the active instances.
2022-12-29 Updated IrrigationController Class
    reworked the load and save functionality, added new helper functions in order to give more flexibility and reuse code
    [IrrigationController.cpp]
2023-01-09 updated IrrigationController Class
    added option to getJSONData from RaspberryPi provided by node red, via http GET method.
2023-01-10 Fixed issue in IrrigationController class
    [IrrigationController.cpp, main.cpp]
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2023-02-11 fixed problem with IrrigationController Class
    [IrrigationController.cpp]
2023-03-17 add MeasuringController Class skeleton
    This Class should handle measuring multiple sensors measure them and upload the results to InfluxDb 2.X
2023-03-19 renamed & updated SensorController class
    Renamed old MeasurementController class & updated the code.
    Built Base class and added closely related subclasses, with different specification.
2023-03-20 Updated Helper functions
    The loading and saving of files to and from SPIFFS has been reworked to ensure compatibility with the new SensorController Class.
    [Helper.h, helper.cpp]
2023-03-20 Updated IrrigationController Class
    The saving and loading functions have been moved to the Helper Class to prevent code duplication.
    [IrrigationController.cpp]
2023-03-20 Fixed issue with SensorController Class
    The function pointer has been removed because it wasn’t working as intended. Lambda functions are now being used to implement the ability to pass an custom measuring function
    [SensorController.cpp]
2023-03-20 Update main.cpp
    - An issue with the watering procedure has been resolved.
    - To reduce code duplication, similar code has been consolidated into functions.
    - A skeleton for the new SensorController Class has been added.
    [main.cpp]
2023-03-21 Updated Helper functions
    - improved older functions
    - renamed and added some more details to some older functions
    - added pubInfluxData functionality to upload sensor values to the DB
2023-03-22 fixed issue, added blinkfunction
    fixed issue when compiling, include of Influxdb needed to habben before connection details.
    added blink function to helper class to give a visual signal of something
    [Helper.h, helper.cpp]
2023-03-22 removing old code from main.cpp
    removing mqtt from the ESP32, it has become obsolete with InfluxDB and Node-red features.
2023-03-23 added Switch-state Controller Class
    A class for controlling switches in the project, with getters and setters for four switch variables
2023-03-24 Updated SwitchController Class
    added method to get config file from network and save states
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2023-03-26 code refactoring & minor fixes
    [SensorController.cpp, SwitchController.cpp, config.h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]
2023-03-30 Removing old layouts
    [bewae3_3_board1v3_6.fzz, bewae3_3_board1v3_7.fzz, bewae3_3_board2v5.fzz]
2023-03-30 Create bewae3_3_board1v3_8.fzz
    Improved design, simplified positioning.
    [bewae3_3_board1v3_8.fzz]
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2023-06-09 fixing issue with circuit, minor rework of sketch
    fixing sens2 pin header issue where it will stay always on and wont be switchable as intended, starting to draw the circuit diagram for better understanding
    [bewae3_3_board1v3_835.fzz, bewae3_3_board3v2.fzz, bewae3_3_board3v22.fzz]
2023-06-10 reworked old code
    fixing multiple issues, preparing for further changes to the code base in order to keep it clean
    [Helper.h, config.h, helper.cpp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]
2023-06-11 fixing typos & improve readability
    [SensorController.cpp, helper.cpp, main.cpp]
2023-06-13 fixing issue with file system & clean up code
    [SwitchController.cpp, config.h, helper.cpp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]
2023-06-16 adding new smaller "one for all board"
    this board is designed for smaller systems and to work with optocoupler modules
2023-06-19 adding reduced circuit version
    [bewae3_3_board5v52.fzz]
2023-06-26 reworked DriverPin classes
    removed solenoid and pump struct and replaced it with a more intuitive and more flexible approach using a new class called LoadDriverPin
    [IrrigationController.cpp, main.cpp]
2023-06-27 fixing issue with IrrigationController
    fixed an issue where instances of the class could be initialized to default,
    fixed an issue which could cause an error on runtime of the program
    [IrrigationController.cpp, config.h, main.cpp]
2023-06-28 fixing issue in IrrigationController
    the name could not be saved correctly
    [IrrigationController.cpp, main.cpp]
2023-06-29 fixing issue with watering procedure
    issue occured sometimes when loading from config it could cause it to fail and produce unreadable group names which lead to further problems
    [IrrigationController.cpp, config.h, main.cpp]
2023-07-02 fixed watering functionality
    added linear decay to activatePWM function to save power and make code more maintainable,
    finally fixed watering phase related problems
    [IrrigationController.cpp, main.cpp]
2023-07-04 deleting old versions
    [bewae3_3_board1v3_835.fzz, bewae3_3_board5v52.fzz]
2023-07-04 adding newest circuit versions
    [bewae3_3_board1v3_838.fzz, bewae3_3_board5v53.fzz]
2023-07-05 changing watering procedure
    changed how the config values are used during procedure, also fixed potential issues when watering only once a day by improving readyTowater function.
    [IrrigationController.cpp, helper.cpp]
2023-07-11 added option to invert shiftregister
    this should allow to use optocoupler which use negative logic
    [Helper.h, config.h, helper.cpp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]
2023-07-11 fixing issue with timetable
    fixing an issue implemented with last rework of this code, where timetable will be ignored and watering will happen every hour
    [IrrigationController.cpp]
2023-07-13 clean up code
    starting clean up, this should help in reworking code later, i want to change the way how watering functionality is handled in main
    [main.cpp]
2023-07-13 fixed issue
    runtime variable 'watering' was not handled correctly, caused it to loop as long as it is set in timetable
    [IrrigationController.cpp, helper.cpp]
2023-07-13 reworked pcb's
    added gerber file for board 5
    removed old version of board 5
    reworked board 1
    [bewae3_3_board1v3_838.fzz, bewae3_3_board5v53.fzz, bewae3_3_board5v5_final.fzz]
2023-07-18 updated sensor handlers
    added more sensor classes for individual sensors,
    changed the constructor to let them initialize directly from json objects
2023-07-26 fixing issue
    sd library could possible conflict when compiling
    [config.h, helper.cpp, main.cpp]
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2023-07-28 changes in Helper Class
    Helper class now acts as an abstraction of the Hardware config.
    In order to support old board versions just an inheritted version of HelperBase class has to be made and set as extern HWHelper at the end of Helper.h file
2023-08-03 fixing issues
    switch controller class json could not be read properly,
    increased sensor file size
    [SwitchController.cpp, config.h]
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2023-08-23 fixed issue with bme module
    [SensorController.cpp]
2023-08-26 fixed issue in http-get & hash functions
    bring back old http-get funciton for testing purposes &
    changing some of the code to make it more readable and fixed issues with hash function when saving files.
    [Helper.h, helper.cpp]
2023-09-13 Improved stability of time functions
    [Helper.h, IrrigationController.cpp, config.h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]
2024-03-04 Clean up files
    This commit removes and renames several files that are no longer needed or have been updated.
    [old-config.txt]
2024-03-13 added simple config web page
    First version of a simple web page to configure the system. It should be hosted with node-red. Import this flow change file paths.
2024-03-27 clarify boards documentation
    clarify what the boards are for and how they are intended
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2024-04-08 fixing error
    when irrigation config was empty it could cause a potential restart
    [Helper.h, helper.cpp, main.cpp]
2024-04-17 Updated process of irrigation state management
    Added a new "running" file where the current state of each group is stored, this should reduce the amount of memory which have to be overwritten each time something get saved back to the "configFile"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
2024-04-19 fixed an issue with file verification
    Updated Synch process from RaspPi, there was an issue. Some files wont be updated correctly when they are different to the local file.
    Fixed calculation of JSON hash, the file size was too small so it produced an empty temp file.
    [config.h, helper.cpp]
2024-04-19 Update main.cpp
    Fixing a endless loop where the controller wont wake again when the RTC was not reachable.
    [main.cpp]
2024-04-20 fixing issues
    Explicitly cast the data from json to its expected datatypes, in Sensor- & SwitchController Class.
    Minor changes in main.cpp, makro paths are now cast to String to use them more dynamic.
    [IrrigationController.cpp, SensorController.cpp, SwitchController.cpp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]
2024-04-22 Updated irrigation process
    fixed a few issues with new implementation of irrigation
    changed getJsonObject function to getJsonDoc, for some reason the old variant caused errors
    added type checks to the expected values from config file
    tested new file which keeps track of current state of the system
    [Helper.h, IrrigationController.cpp, helper.cpp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]
2024-05-30 Update bewaeConfigPageFlow.json
    new config page, allows for more devices been configured.
    Simplify process of get request for device configuration.
    Added a dedicated backend routine to get and save config.
2024-05-30 Update bewaeConfigPageFlow.json
    fixed issues with: add/save/delete devices from main page, updated function with selector.
2024-06-01 fixing error
    Path would macros not allow proper file reads from server. Should be fixed now while maintaining old path functionality with local file management.
    [config.h, helper.cpp]
